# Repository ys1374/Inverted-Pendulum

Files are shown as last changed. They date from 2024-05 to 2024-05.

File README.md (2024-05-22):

The importance of automatic control in industries and everyday life is undeniable, and it can be said that 
automatic control systems are among the most important parts of today's advanced industries. In this 
project, we will pose a question and use tools such as dynamics and control science to find a satisfactory 
answer. Although this question has been repeatedly addressed in the field of control science and has 
received satisfactory answers, the nature of science and scientific methods is reproducibility. We aim to 
reproduce an answer to this issue in both theoretical and practical states. The question is: 
"How can the relative angle of a satellite carrier to the ground be controlled?" 
The need to pose such a question arises when you want to actively control the satellite carrier's angle 
relative to the ground to eliminate the effects of unmeasurable and unpredictable external factors such 
as wind or gravity. This can be done in two ways: one is using side fins, which will consume a lot of fuel 
since satellite carriers usually have to move at angles other than 90 degrees to the ground. Weight is 
always a critical factor for the satellite carrier's range. The other method is thrust vector control, which 
is the method examined in this project. In this project, we first define the satellite carrier model and 
derive the equations describing the satellite carrier's motion, then we use control science to control the 
main variable, i.e., the satellite carrier's angle relative to the ground.

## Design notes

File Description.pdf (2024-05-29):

### 1 Table of Contents

### 2 Introduction

The importance of automatic control in industries and everyday life is undeniable, and it can be said that automatic control systems are among the most important parts of today's advanced industries. In this project, we will pose a question and use tools such as dynamics and control science to find a satisfactory answer. Although this question has been repeatedly addressed in the field of control science and has received satisfactory answers, the nature of science and scientific methods is reproducibility. We aim to reproduce an answer to this issue in both theoretical and practical states. The question is:

"How can the relative angle of a satellite carrier to the ground be controlled?"

The need to pose such a question arises when you want to actively control the satellite carrier's angle relative to the ground to eliminate the effects of unmeasurable and unpredictable external factors such as wind or gravity. This can be done in two ways: one is using side fins, which will consume a lot of fuel since satellite carriers usually have to move at angles other than 90 degrees to the ground. Weight is always a critical factor for the satellite carrier's range. The other method is thrust vector control, which is the method examined in this project. In this project, we first define the satellite carrier model and derive the equations describing the satellite carrier's motion, then we use control science to control the main variable, i.e., the satellite carrier's angle relative to the ground.

### 3 Satellite Carrier Model

In this project, we consider the model as a pendulum representing the satellite carrier. This model provides a reasonably accurate approximation due to similar geometric features (one dimension being significantly larger than the other two) and a nearly balanced mass distribution along the pendulum length. For the forces exerted on the satellite carrier due to thrust vector changes, we consider a cart or carrier. Here, for simplicity in providing rotational force with common motors in the market compared to the linear motion of the cart requiring a rail and force transmission process, we consider the cart as a carrying rod and connect the pendulum to the carrying rod via an encoder (an encoder measures the angle error of the pendulum relative to the ground or the feedback sensor). The carrying rod plays the role of the cart and provides the force exerted on the satellite carrier due to thrust angle changes via a DC motor. Obviously, in this project, we consider the problem in 2D, but the results can be easily generalized to the real 3D state.

### 4 Derivation of Equations

### 4.1 Pendulum

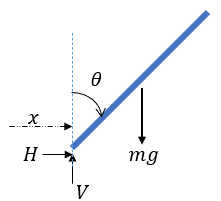
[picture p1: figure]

Figure 1

Pendulum lengtℎ = 2L

xg = x + Lsinθ | (1)
yg = Lcosθ | (2)
Jθ̈= ∑ T | (3)
max = H | (4)
may = V − mg | (5)

max = H → m

d

2xg
dt

2 = H

(1)
→ | mẍ+ m(Lsinθ)
'' = H | (6)

may = V − mg → m

d

2yg
dt

2 = V − mg

(2)
→ | 0 = V − mg | (7)

Since we write the rod rotation equation around its center of mass and there is complete symmetry around the center of mass, J = 0. Therefore, equation (3) with the help of equation (7) is summarized as equation (8):

J = 0

(3)
→ | 0 = ∑T → | 0 = HLcosθ − VLsinθ

(7)
→ H = mg

sinθ
cosθ

(8)

Now, we write the torques around the center of mass, resulting in the simplification of equation (3) as equation (9):

ẍ+ L(sinθ)

'' = g

sinθ
cosθ

(9)

### 4.2 Rod

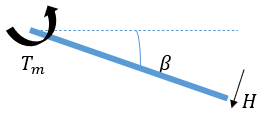
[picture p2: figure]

Figure 2

Rod lengtℎ = L

′

Jβ̈+ b0β̇ = ∑ T (10)

In equation (10), the friction coefficient b0 is considered for mechanical friction.

x = βL

′
(11)

### 4.3 DC Motor

Figure 3

La

dia
dt + Raia + Kbβ̇ = ea
(12)

In cylindrical DC motors (cross-section significantly smaller than length), La can be approximated as zero, making the equation a second-order function and simplifying the solution. Also, in these DC motors, the torque and back EMF constants are equal.

La = 0
Tm = KTia | (13)
Kb = KT = K
Raia + Kβ̇ = ea
| (14)

### 4.4 Motor and Rod Assembly

(10), (11) → Jβ̈+ b0β̇ = Tm − HL ′

(13)
→

J
K

β̈+

b0
K

β̇ +

HL

′
K

= ia (15)

(14), (15) → Ra(Jβ̈+ b0β̇ + HL
′
) + K

2β̇ = Kea → RaJβ̈+ (Rab0 + K
2

)β̇ + RaL
′H = Kea

→ RaJβ̈+ (Rab0 + K
2

)β̇ + RaL
′
(mẍ+ mL(sinθ)

'') = Kea →

RaJβ̈+ (Rab0 + K
2

)β̇ + RaL

′2
mβ̈+ RamLL
′
(sinθ)

'' = Kea →

(RaJ + RaL

′2
m)β̈+ (Rab0 + K
2

)β̇ + RamLL
′
(sinθ)

'' = Kea (16)

### 4.5 System Characteristic Equations (Nonlinear Equations)

L

′β̈+ L(sinθ)
'' = g

sinθ
cosθ (9)

(RaJ + RaL

′2
m)β̈+ (Rab0 + K
2

)β̇ + RamLL
′
(sinθ)

'' = Kea (16)

(sinθ)

'' = θ̈cosθ − θ̇sinθ (17)

(9)

(17)
→ L

′β̈+ Lθ̈cosθ − Lθ̇sinθ = g

sinθ
cosθ (18)

(16)

(17)
→ | (RaJ + RaL

′2
m)β̈+ (Rab0 + K
2

)β̇ + RamLL
′θ̈cosθ − RamLL

′θ̇sinθ = Kea (19)

(18) → θ̈=

gsinθ
Lcos²θ

+

sinθ
cosθ θ̇ −

L

′
Lcosθ β̈ (20)
(19) → β̈=

K
RaJ+RaL

′

2m

ea −

(Rab0+K

2
)
RaJ+RaL

′

2m

β̇ −

RamLL

′

RaJ+RaL

′

2m

θ̈cosθ +

RamLL

′

RaJ+RaL

′

2m

θ̇sinθ (21)

(20), (21) →

θ̈=

gsinθ
Lcos²θ

+

sinθ
cosθ θ̇

−

L

′
Lcosθ (
K
RaJ + RaL

′2m

ea −

(Rab0 + K

2
)
RaJ + RaL

′2m

β̇ −

RamLL

′
RaJ + RaL

′2m

θ̈cosθ

+

RamLL

′
RaJ + RaL

′2m

θ̇sinθ )

(21), (20) →

β̈=

K
RaJ + RaL

′2m

ea −

(Rab0 + K

2
)
RaJ + RaL

′2m

β̇ −

RamLL

′
RaJ + RaL

′2m

(
gsinθ
Lcosθ + θ̇sinθ −

L

′
L

β̈)

+

RamLL

′
RaJ + RaL

′2m

θ̇sinθ

Simplification

θ̈=

gsinθ
Lcos²θ

+

sinθ
cosθ θ̇ −

KL

′
L(RaJ + RaL

′2m)

ea
cosθ +

L

′
(Rab0 + K

2
)
L(RaJ + RaL

′2m)

β̇
cosθ +

RamL

′2

RaJ + RaL

′2m

θ̈

−

RamL

′2

RaJ + RaL

′2m

θ̇sinθ
cosθ

β̈=

K
RaJ + RaL

′2m

ea −

(Rab0 + K

2
)
RaJ + RaL

′2m

β̇ −

gRamL

′
RaJ + RaL

′2m

sinθ
cosθ −

RamLL

′
RaJ + RaL

′2m

θ̇sinθ

+

RamL

′2

RaJ + RaL

′2m

β̈+

RamLL

′
RaJ + RaL

′2m

θ̇sinθ

Simplification

θ̈=

RaJ + RaL

′2
m
RaJ

gsinθ
Lcos²θ

−

θ̇sinθ
cosθ −

KL

′
RaJL

ea
cosθ +

L

′
(Rab0 + K

2
)
RaJL

β̇
cosθ

β̈=

K
RaJ

ea −

(Rab0 + K

2
)
RaJ

β̇ −

gmL

′
J

sinθ
cosθ −

mLL

′
J

θ̇sinθ +

mLL

′
J

θ̇sinθ

Simplified characteristic equations (nonlinear equations):

θ̈ =

J + L

′2
m
J

gsinθ
Lcos²θ

−

θ̇sinθ
cosθ −

KL

′
RaJL

ea
cosθ

+

L | ′ | 2 | ) | β̇
(Rab0 | + K
RaJL

cosθ

(22)

β̈ | =
K | 2 | ) | gmL | ′ sinθ
RaJ

ea −

(Rab0 + K
RaJ

β̇ −
J

cosθ

(23)

We use equations (22) and (23) to plot the pendulum and demonstrate its motion in MATLAB.

### 4.6 System Characteristic Equations (Linear Equations)

Linearization of equations (22) and (23):

Assumption: sinθ = θ , cosθ = 1 , θθ̇ = 0

θ̈ =

g(J + L

′2
m)
LJ θ +

L

′
(Rab0 + K

2
)
LRaJ

β̇ −

KL

′
LRaJ

ea

(24)

β̈ = −

gmL

′
J

θ −

(Rab0+K²)

̇
RaJ

β̇ +

K
RaJ

ea

(25)

θ̈ = A1 θ + A2 β̇ + B1 ea
(26)
β̈= A3 θ + A4 β̇ + B2 ea
(27)

A1 =

g(J + L

′2
m)
LJ | A1 =

g(J + L

′2
m)
LJ

A3 = −

gmL

′
J

A4 = −

(Rab0 + K

2
)
RaJ | B1 = −

KL

′
LRaJ

B2 =

K
RaJ

### 4.7 State-Space Equations (Linear Equations)

To design the controller, we first convert the equations to their state-space form and obtain the system in state-space representation. Therefore, from equations (26) and (27), we have:

ẋ = Ax + Bea | (28)
ẋ = [

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
] x + [

0
B1
0
B2

] ea
| (29)

ẋ = [

x1̇
x2̇
x3̇
x4̇

] = [

x2
θ̈
x4
β̈

] x = [

θ
θ̇
β
β̇

] = [

x1
x2
x3
x4

] A = [

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
] | B = [

0
| B1
0
| B2

]

### 5 Fabrication of the dynamic model

### 5.1 Specifications of the Fabricated model

L

′ = 0.28 m | #Rod length
L = 0.11 m | #half Pendulum length
g = 9.81 | #Gravity constant

K =

0.588
7.8
N. m A | #DC motor torque constant
Ra = 3 Ω | # DC motor resistance
b0 = 0.1 | #Mechanical resistance
m = 0.039 Kg | # Pendulum weight

### 5.2 Components used

The following components were used in the construction of this project:

1) 24V DC servo motor, model Yaskawa UGFMED-B5LGR51
2) Arduino Mega 2560
3) Autonics 2500 pulse encoder
4) DC motor driver 43A 27V, model BTS7960
5) 12V power supply (Arduino power supply)
6) 24V 10A power supply
7) Breadboard
8) Mounting plates and connecting rods

### 5.3 State-space equations for the real model (linear equations)

From equations (26) and (27) and obtaining their coefficients, we have:

ẋ = [

0
102.75
0
−5.33

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
| 12.9
| 1 −5.07 ] x + [
| 0
| 3.18
| 0 −1.25

] ea

A1 = 102.75 | A2 = 12.9 | A3 = −5.33 | A4 = −5.07 | B1 = 3.18 | B2 = −1.25

### 5.4 Fabrication Challenges

During the construction of the project, we encountered several issues which I'll detail here.

1) Encoder Signal: The signal B from the encoder, which represents the theta feedback (angle of the pendulum), was a square wave signal that reached a maximum approximate voltage of 1.7 volts. However, Arduino considers a minimum of 3 volts for high signals (or logic level '1'). Due to this voltage difference, Arduino couldn't accurately detect the angle or direction of rotation. This issue was resolved by adding a 1.5V AAA battery to compensate for the voltage difference.

2) Arduino Uno Limitations: Initially, we used the Arduino Uno controller, which, due to having only one pair of signal inputs for the encoder, couldn't provide a solution to our problem. This limitation was overcome by replacing it with the Arduino Mega controller.
3) Length of Lever Arm: The significant length of the lever arm caused increased sensitivity in the motor operation, leading to motor inertia issues. By minimizing the length of this lever arm, we were able to mitigate this problem.
4) Angular Refresh Rate: One fundamental issue we faced was the refresh rate of the pendulum angle. By reducing the refresh time to 1 millisecond, we initially achieved active control. However, these changes had an irreversible negative impact on the motor driver. With a refresh rate of 1 millisecond, the right-side H-bridge of the motor driver completely failed. This issue was resolved by replacing the motor driver and increasing the refresh rate to 10 milliseconds.

### 5.5 Wiring diagram of the constructed model

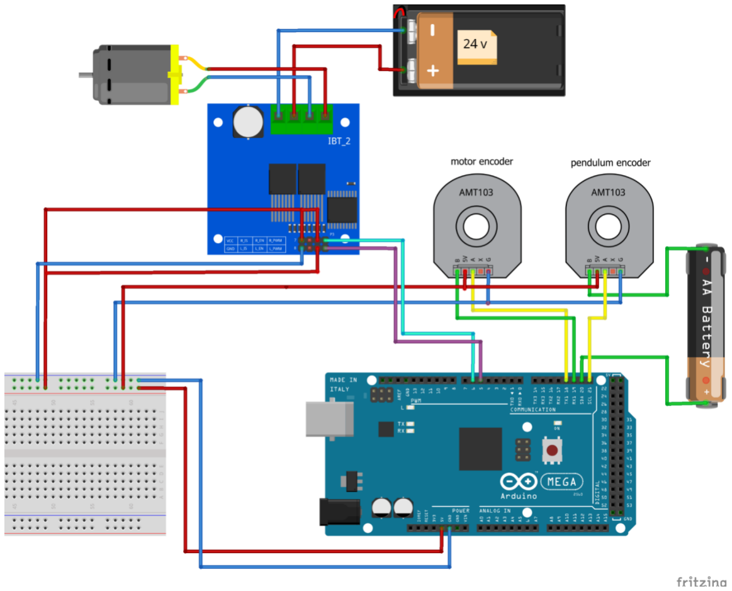
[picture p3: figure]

Figure 4

### 6 Simulation

### 6.1 Root Locus Analysis

The Root Locus Analysis of the closed-loop poles of the system can be observed in Figure 5.

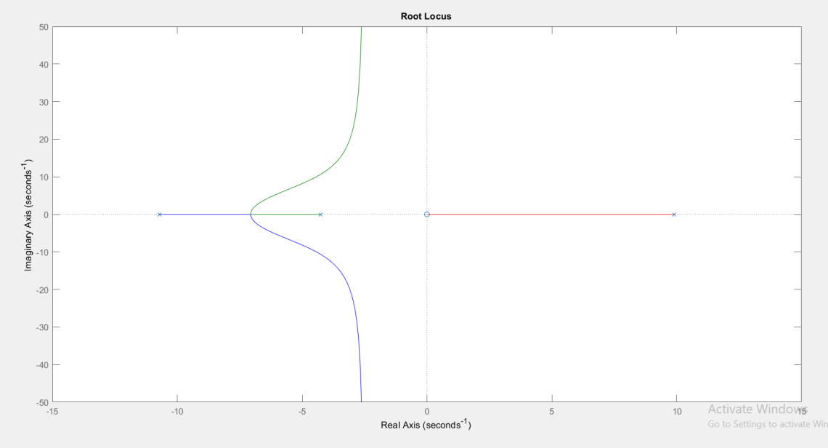
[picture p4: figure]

Figure 5*

* Figure 5* is obtained from the MATLAB code in the attached file root_locus.m.

The Fabricated Model has 4 poles at [0, 9.91, -10.72, -4.26] and two zeros at [0, 0].

### 6.2 Proportional Controller

We will use proportional control using state-space, where the controller coefficients are obtained from the LQR method with cost functions and weights (R) and (Q). With this method, we obtain 4 coefficients for the controller, each corresponding to its respective state variable ((θ, θ̇

, β, β̇)). In state
feedback, we feedback the variables and compare them with their desired values, then subtract them. Afterwards, we multiply this difference by the control coefficients. This process generates the necessary control force signal to control the system or neutralize disturbances.

To visualize the position and response of the system in MATLAB, we use two functions: `nonlinear_sys.m` and `print_sys.m`, which encompass the characteristic functions of the nonlinear system. The files are attached. You can also refer to the MATLAB file `system.m` to see how the pendulum moves and execute it.

The folloing figures demonstrate this design.

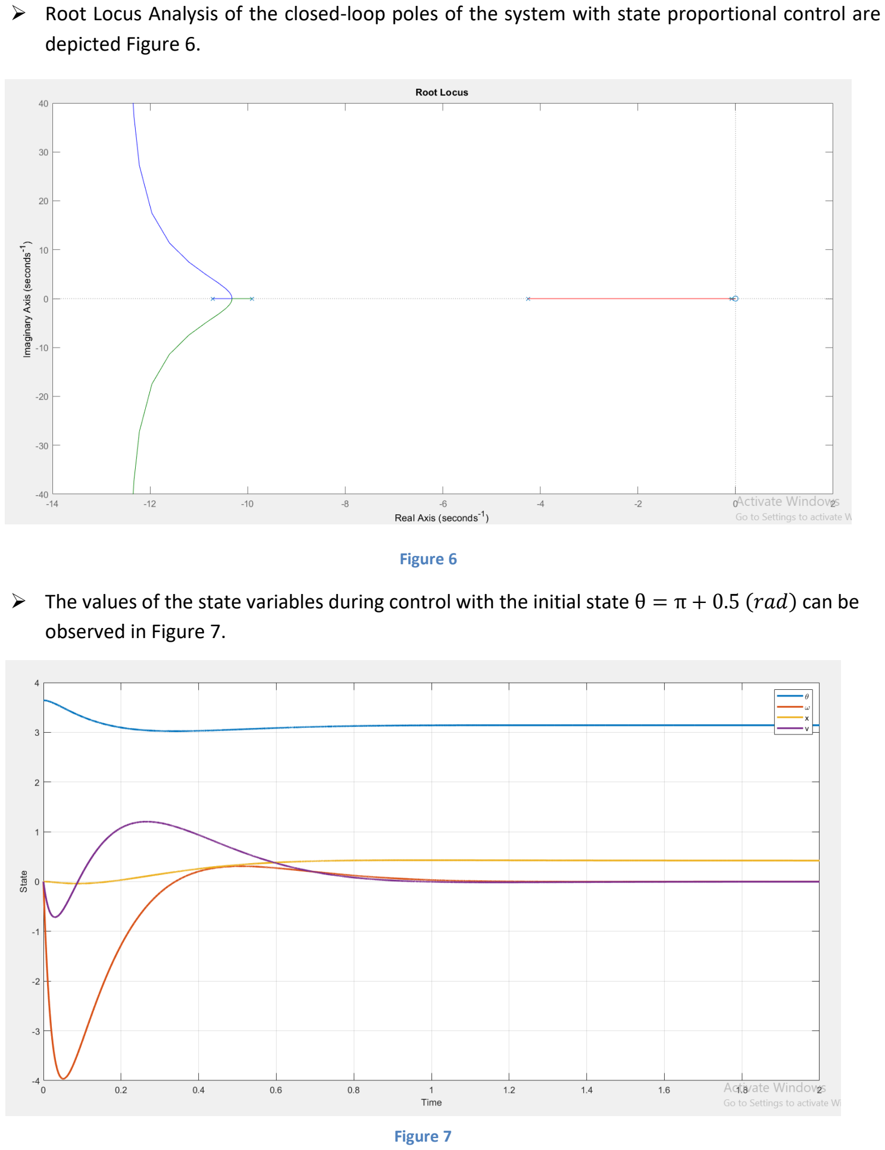
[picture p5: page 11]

- Root Locus Analysis of the closed-loop poles of the system with state proportional control are depicted Figure 6.

Figure 6

- The values of the state variables during control with the initial state θ = π + 0.5 (rad) can be observed in Figure 7.

Figure 7

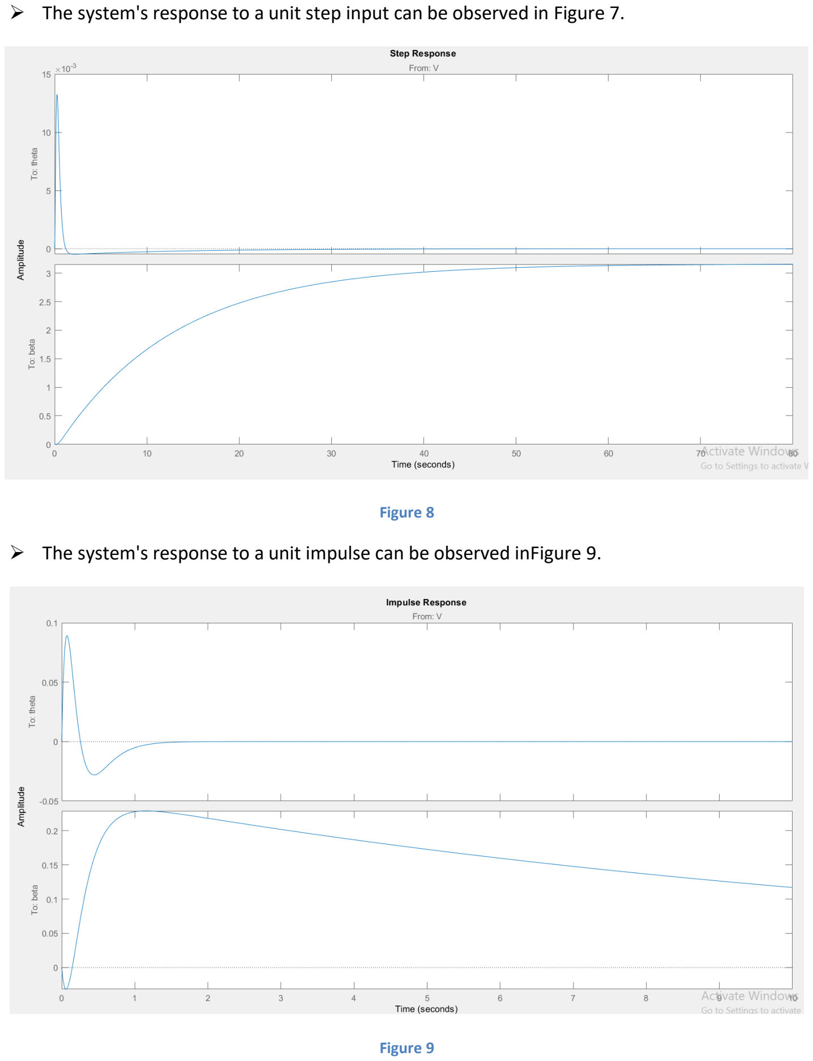
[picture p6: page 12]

- The system's response to a unit step input can be observed in Figure 7.

Figure 8

- The system's response to a unit impulse can be observed inFigure 9.

Figure 9

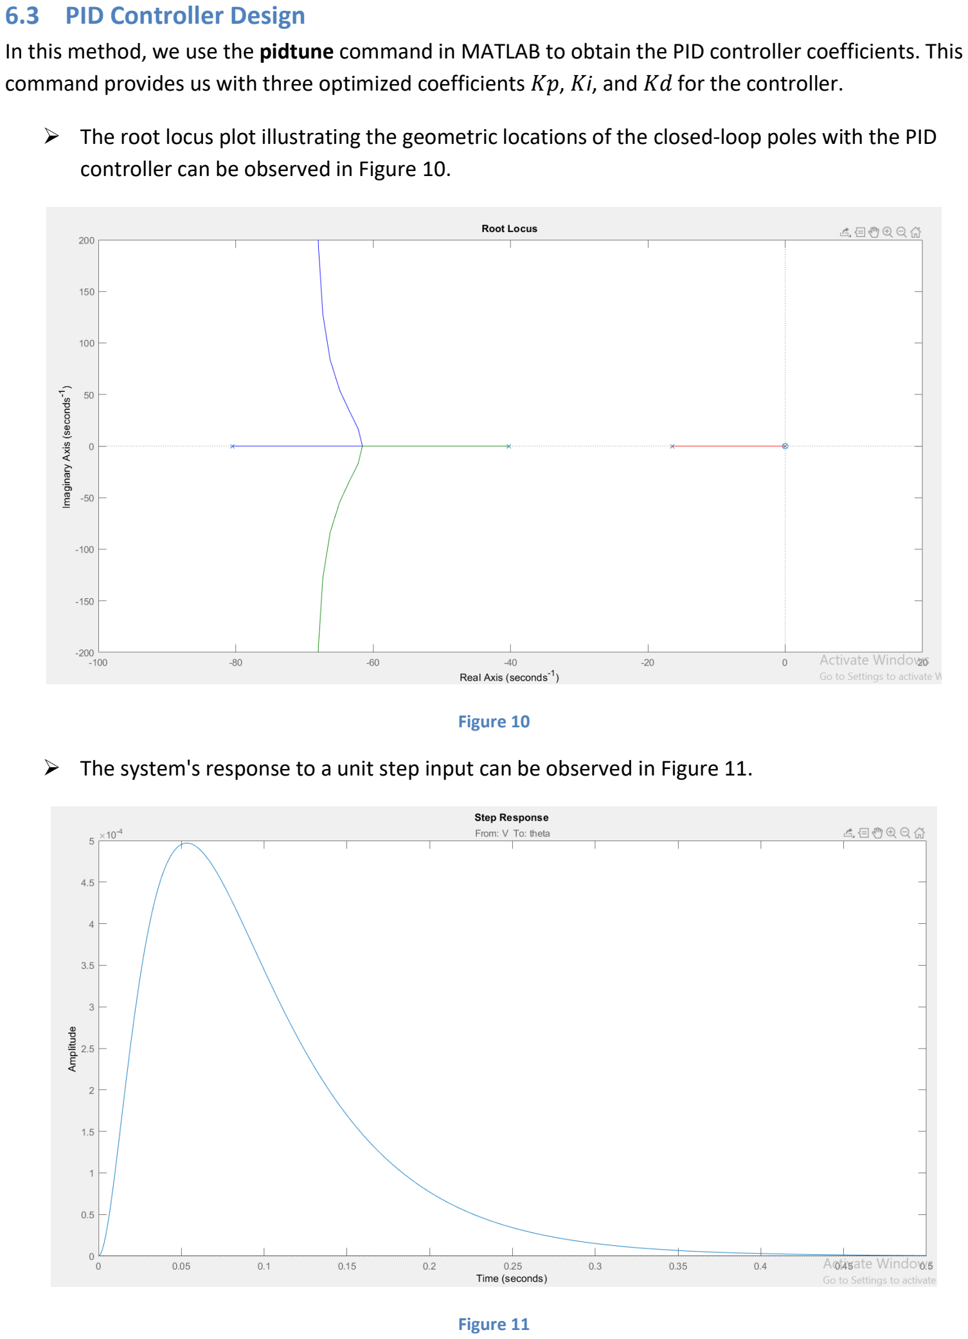
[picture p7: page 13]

### 6.3 PID Controller Design

In this method, we use the pidtune command in MATLAB to obtain the PID controller coefficients. This command provides us with three optimized coefficients Kp, Ki, and Kd for the controller.

- The root locus plot illustrating the geometric locations of the closed-loop poles with the PID controller can be observed in Figure 10.

Figure 10

- The system's response to a unit step input can be observed in Figure 11.

Figure 11

- The system's response to a unit impulse can be observed in Figure 12.

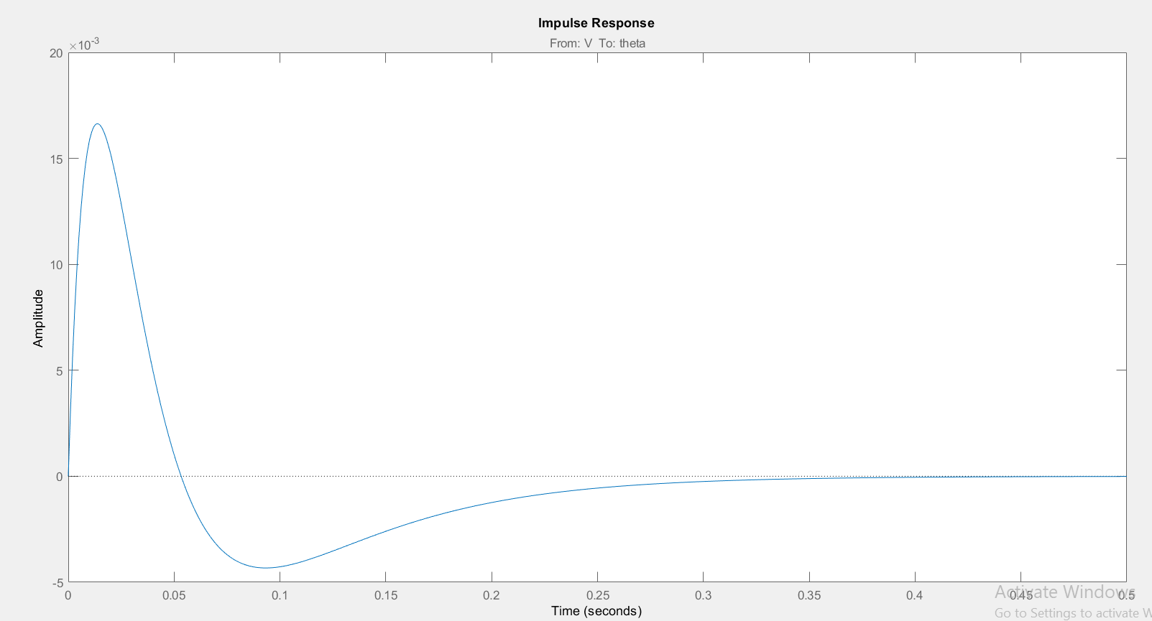
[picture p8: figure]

Figure 12

### 7 Conclusion

Initially, we modeled the satellite carrier into a more accessible model, like an inverted pendulum. Then, using the dynamics equations of the pendulum, we simulated the applied force through angle adjustment of the thrusters using a rod and a DC motor model. We extracted the equations for both through dynamics and electrical machinery. Now, we have access to the controller's tuning function, namely the motor voltage, and the output, namely the pendulum angle. We then proceed to design the controller. The controller we use is PID, and we obtained its three coefficients using the `pidtune` command in MATLAB. Now, it's time to apply this controller to our constructed dynamic model. We apply the three controller coefficients using the PID Arduino library to the Mega Arduino controller, and we observe that the controller effectively maintains the carrier upright. In this project, we have achieved our desired outcome, which is reproducing the response given to the carrier angle control.

### 8 References

[1]Steven L. Brunton, J. Nathan Kutz - Data-Driven Science and Engineering_ Machine Learning, Dynamical Systems, and Control-Cambridge University Press (2019)

[2] Dynamics / J. L. Meriam, L. G. Kraige, Virginia Polytechnic Institute and State University, J. N. Bolton, Bluefi eld State College.—Eighth edition.
[3] Modern Operating Systems By Andrew S. Tanenbaum(5th Edition) by Katsuhiko Ogata, Andrew S. TanenbaumHardcover, 912 Pages, Published 2009 by Prentice Hall

[4] Advanced Engineering Mathematics, 10th Edition by ERWIN KREYSZIG, HERBERT KREYSZIG,New York, New York,EDWARD J. NORMINTON,Associate Professor of Mathematics, Carleton UniversityProfessor of Mathematics,Ohio State UniversityColumbus , JOHN WILEY & SONS, INC.
[5] James K. Roberge. The mechanical seal. Bachelor's thesis, Massachusetts Institute of Technology, May 1960.
[6] Differential Equations", Dr. Masoud Nikoukar, Azadeh Publications, AmirKabir University of Technology.

### 9 Appendix

1) \Arduino code\inverted_pendulum.ino
2) \Matlab code\noneliniar_sys.m
3) \Matlab code\print_sys.m
4) \Matlab code\root_locus.m
5) \Matlab code\sys2.m
6) \Matlab code\system.m
7) \Matlab code\system_pid.m

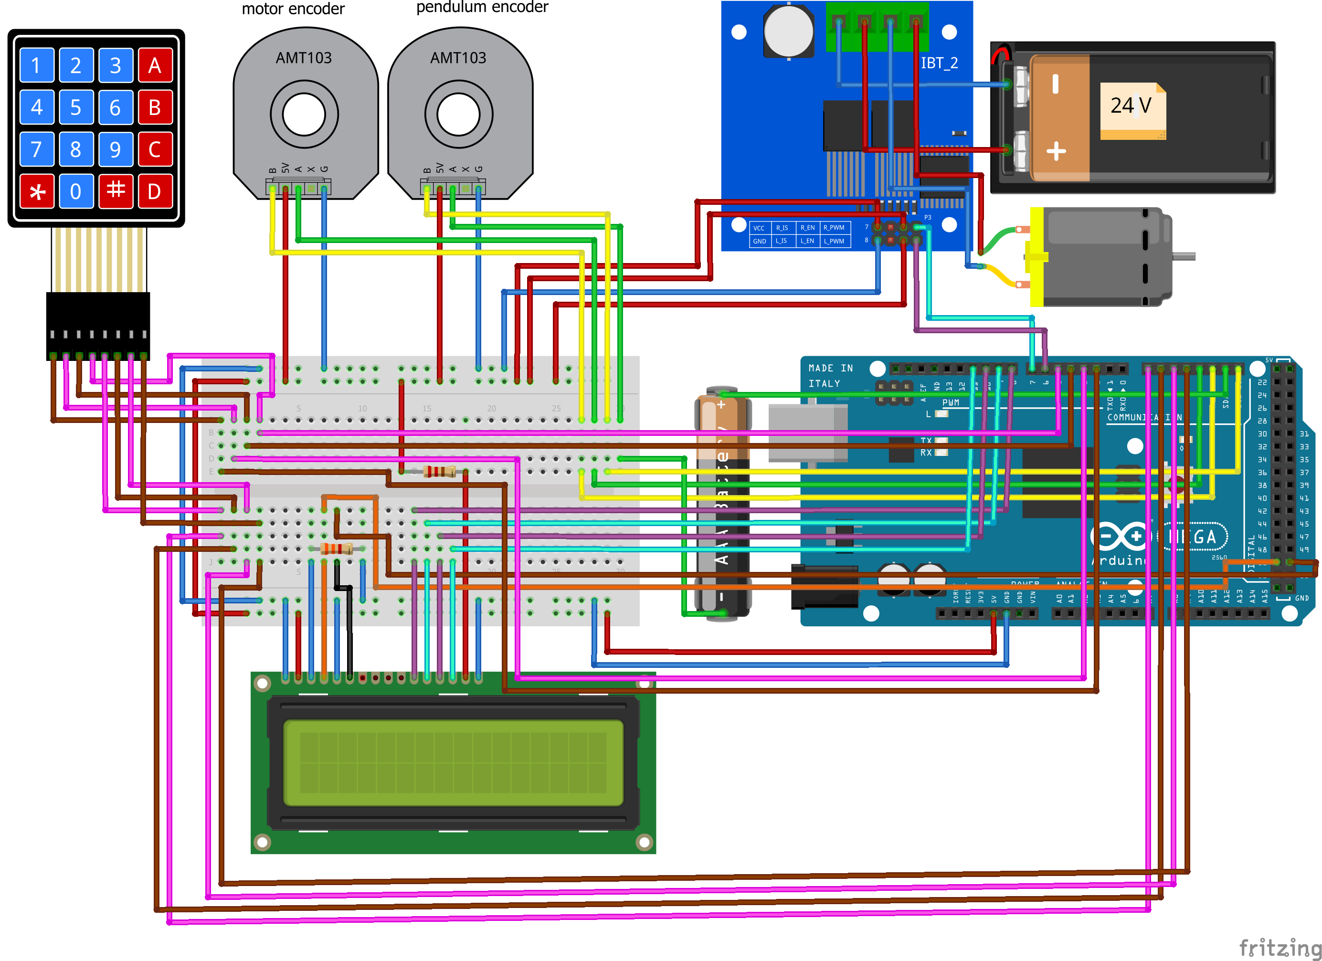
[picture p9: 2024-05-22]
PDF photo/Untitled Sketch_bb.png

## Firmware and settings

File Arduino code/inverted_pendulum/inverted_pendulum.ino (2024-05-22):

// !!!!!!!!!!!!!!!!DO NOT CHANGE ANYTHING !!!!!!!!!!!!!!
// © 2021 All rights reserved for Yasin Salehi
//if you change even a dot in this script
//i won't stay down i'll bring you to marshall court
//and i beat you there then i will feed you to the SHARKS!!!!!
//HA HA HA HA HA ....  
//oh my god did you just believe that?
//HA HA HA HA HA ....
//i'm so funny oh lord...
//pardon my sense of humor of course you can change anything 
//but i recommendyou not to do so
//i wrote the script myself and now i don't even know what is it about
//anyway if you made any improvement by NOT CHANGEING the script
//feel free to write to me
//salehi.yasin@gmail.com
//Salehi-REGARDS
//stay safe - wear mask
























//-----------------------------------------------------
#include <Encoder.h>
#include <PID_v1.h>
#include <LiquidCrystal.h>
#include <Keypad.h>

char hexaKeys[4][4] = {  {1, 2, 3, 13}, {4, 5, 6, 14}, {7, 8, 9, 15}, {11, 10, 12, 16}};
byte rowPins[4] =  {14, 15, 16, 17};
byte colPins[4] = {2, 3, 4, 5};
const int m = 5;
const int n = m - 1;
int k_triger = 0;
int cruser_column;
int chose = 0;

double theta = 0;
double theta_Setpoint = 0;
double Voltage;
double theta_kp, theta_ki, theta_kd;
double beta = 0;
double beta_Setpoint = 0;
double beta_kp = 1.25, beta_ki = 0, beta_kd = .1;

int time1 = 11;

Encoder pend_encoder(18, 19);
Encoder rod_encoder(20, 21);

PID theta_controller(&theta, &Voltage, &theta_Setpoint, theta_kp, theta_ki, theta_kd, DIRECT);
PID beta_controller(&beta, &theta_Setpoint, &beta_Setpoint, beta_kp, beta_ki, beta_kd, DIRECT);

LiquidCrystal lcd(50, 51, 8, 9, 10, 11);

Keypad customKeypad = Keypad(makeKeymap(hexaKeys), rowPins, colPins, 4, 4);

void setup() {

  Serial.begin(115200);

  lcd.begin(20, 4);

  pinMode(6, OUTPUT);
  pinMode(7, OUTPUT);

  lcd_first_print();
  defult_chose();
  controller_asignment();
    lcd.clear();
  while (time1 > 0) {
    time1 = time1 - 1;
        
    lcd.setCursor(4, 0);
    lcd.print("**WARNING**");
    lcd.setCursor(2, 1);
    lcd.print("The Process will");
        lcd.setCursor(6, 2);
    lcd.print("start in");
    lcd.setCursor(9, 3);
    lcd.print(time1);
    delay(1000);
    lcd.clear();
  }

  pend_encoder.write(5000);
  rotation_180();

    lcd.setCursor(4, 0);
    lcd.print("**WARNING**");
    lcd.setCursor(2, 1);
    lcd.print("Please DO NOT let");
        lcd.setCursor(0, 2);
    lcd.print("full cycle rotation");
    lcd.setCursor(5, 3);
    lcd.print("DISTURB IT");


}
void loop() {

  theta = pend_encoder.read();
  beta = rod_encoder.read();


  if (-1000 < theta & theta < 1000)
  {
    theta_controller.Compute();

    assign_Voltage_fun(Voltage);
    print_simple();

  }
  else
  {

    turn_stop();//-----------------------------------------
  }
}
//********************************************************************************
//***************************FUNCTIONS 1st part***********************************
//********************************************************************************

void turn_cw(int value) {
  analogWrite(6, value);
  analogWrite(7, 0);
}

void turn_ccw(int value) {
  analogWrite(6, 0);
  analogWrite(7, value);
}

void turn_stop() {
  analogWrite(6, 0);
  analogWrite(7, 0);
}
//--------------------------------
void assign_Voltage_fun(double Voltage_fun) {
  if (Voltage_fun < 1 & Voltage_fun > -1) {
    turn_stop;
  }
  if (Voltage_fun >= 1) {
    turn_cw(Voltage_fun);
  }
  if (Voltage_fun <= -1) {
    turn_ccw(abs(Voltage_fun));
  }
}
//------------------------------------
void print_simple() {
  Serial.print(theta) ;
  Serial.print("|||||||") ;
  Serial.print(beta) ;
  Serial.print("|||||||") ;
  Serial.print(theta_Setpoint) ;
  Serial.println("") ;
}
//------------------------------------
void rotation_180() {
  pend_encoder.write(5000);
  int theta_func;
  int beta_func;
  theta_func = pend_encoder.read();
  while (theta_func < 9000 &  theta_func > 1000) {
    theta_func = pend_encoder.read();
    beta_func = rod_encoder.read();

    while (beta_func != 50) {
      beta_func = rod_encoder.read();
      turn_cw(80);

      theta_func = pend_encoder.read();
      if (theta_func == 9000 || theta_func == 1000) {
        if (theta_func == 9000) {
          pend_encoder.write(-1000);
        }
        if (theta_func == -9000) {
          pend_encoder.write(1000);
        }
        return;
      }
    }

    while (beta_func != 0) {
      beta_func = rod_encoder.read();
      turn_ccw(200);
      theta_func = pend_encoder.read();
      if (theta_func == 9000 || theta_func == 1000) {
        if (theta_func == 9000) {
          pend_encoder.write(-1000);
        }
        if (theta_func == -9000) {
          pend_encoder.write(1000);
        }
        return;
      }
    }

  }
}
//------------------------------------------------------
void controller_asignment() {
  theta_controller.SetMode(AUTOMATIC);
  theta_controller.SetOutputLimits(-255, 255);
  theta_controller.SetSampleTime(10);
  theta_controller.SetTunings(theta_kp, theta_ki, theta_kd);

  beta_controller.SetMode(AUTOMATIC);
  beta_controller.SetOutputLimits(-150, +150);
  beta_controller.SetSampleTime(3);
  beta_controller.SetTunings(beta_kp, beta_ki, beta_kd);
}

//********************************************************************************
//***************************FUNCTIONS 2nd part***********************************
//********************************************************************************

//FUNCTION read k value from keypad  --------------------------------------------
double k(int cruser_row) {
  double k1, k2, k;
  int k1_digits[m] = {0};
  int k1_digits_old[m] = {0};

  int k2_digits[m] = {0};
  int k2_digits_old[m] = {0};

  int oldkey  = 0;
  int exit_1  = 0;
  int dot_key = 0;
  int p = 0;
  int lcd_cruser = 4;


  while (exit_1 == 0) {

    int Key_k = customKeypad.getKey();

    if (Key_k != 0 & Key_k == 12) {
      exit_1 = exit_1 + 1;
      Serial.println("12 is pushed");
      delay(500);
    }
    if (Key_k != 0  & Key_k == 11) {
      lcd.setCursor(lcd_cruser, cruser_row);
      lcd.print(".");
      dot_key = dot_key + 1;
      Serial.println("11 is pushed");
      delay(500);
    }


    // >1 digits---------------------------------------------------
    if (Key_k != 0 & dot_key == 0) {

      //push 1-9 number keys(key 1-9)------------------------------
      if (Key_k < 10) {
        lcd.setCursor(lcd_cruser, cruser_row);
        lcd.print(Key_k);
        k1_digits[0] = Key_k;

        for (int i = 0; i < n ; i++) {
          k1_digits[i + 1] = k1_digits_old[i];
        }


        for (int j = 0; j < n + 1 ; j++) {
          k1_digits_old[j] = k1_digits[j];
        }


        for (int t = 0; t < n + 1; t++) {
          Serial.print(k1_digits[p]);
        }
        Serial.println("");

      }
      //push 0 number (key 10)------------------------------
      if (Key_k == 10) {
        k1_digits[0] = 0;
        lcd.setCursor(lcd_cruser, cruser_row);
        lcd.print(0);
        for (int i = 0; i < n ; i++) {
          k1_digits[i + 1] = k1_digits_old[i];
        }


        for (int j = 0; j < n + 1 ; j++) {
          k1_digits[j] = k1_digits_old[j];
        }


        for (int t = 0; t < n + 1; t++) {
          Serial.print(k1_digits[p]);
        }
        Serial.println("");

      }
      //--------------------------------------------------------
      k1 = k_1(k1_digits);
      delay(500);
      lcd_cruser = lcd_cruser + 1;

    }
    // 0< <1 digits------------------------------------------------------
    if (Key_k != 0  & dot_key == 1) {

      //push 1-9 number keys(key 1-9)------------------------------
      if (Key_k < 10) {

        lcd.setCursor(lcd_cruser, cruser_row);
        lcd.print(Key_k);

        k2_digits[p] = Key_k;
        p = p + 1;

        for (int i = 0; i < n + 1; i++) {
          Serial.print(k2_digits[i]);
        }
        Serial.println("");


      }
      //push 0 number (key 10)------------------------------
      if (Key_k == 10) {

        k2_digits[p] = 0;
        p = p + 1;

        lcd.setCursor(lcd_cruser, cruser_row);
        lcd.print(0);

        for (int i = 0; i < n + 1; i++) {
          Serial.print(k2_digits[i]);
        }
        Serial.println("");

      }
      //--------------------------------------------------------
      k2 = k_2(k2_digits);
      delay(500);
      lcd_cruser = lcd_cruser + 1;

    }
    //--------------------------------------------------------------
  }

  k =  k1 + k2;

  return k;

}
//FUNCTION tunrn digits to number for >1 numbers--------------------------------------------------------------
int k_1(int k_11[m]) {
  float num = k_11[0] + (k_11[1] * 1e1) + (k_11[2] * 1e2) + (k_11[3] * 1e3) + (k_11[4] * 1e4);
  return num;
}
//FUNCTION tunrn digits to number for 0< <1 numbers----------------------------------------------------------
double k_2(int k_22[m]) {
  double num;
  //  if (k_22[0] == 0 & k_22[1] == 0 & k_22[2] == 0 & k_22[3] == 0 & k_22[4] == 0) {
  //    return num = 0.0;
  //  }

  num = (k_22[0] / 1e1) + (k_22[1] / 1e2) + (k_22[2] / 1e3) + (k_22[3] / 1e4) + (k_22[4] / 1e5);
  return num;
}
//FUNCTION lcd first print -----------------------------------------------------------------------------------
void lcd_first_print() {
  lcd.setCursor(0, 0);
  lcd.print("B.Sc. Final Proj. of");

  lcd.setCursor(0, 2);
  lcd.print("YASIN SALEHI");

  lcd.setCursor(0, 3);
  lcd.print("1398-1400");

  delay(7000);
  lcd.clear();
  lcd.setCursor(0, 0);
  lcd.print("Donated to");

  lcd.setCursor(0, 2);
  lcd.print("Kurdistan University");


  delay(5000);
  lcd.clear();
  lcd.setCursor(0, 0);
}
//FUNCTION get k values -----------------------------------------------------------------------------------
void get_k_values() {
  lcd.setCursor(0, 0);
  lcd.print("Please Enter K Gain ");
  lcd.setCursor(0, 1);
  lcd.print("Values");
  delay(3000);
  lcd.clear();

  if (k_triger == 0) {
    cruser_column = 0;
    lcd.setCursor(15, cruser_column); lcd.print("*10^3");
    lcd.setCursor(0, cruser_column);
    lcd.print("Kp=");
    theta_kp = k(cruser_column);
    k_triger = k_triger + 1;
    Serial.println(""); Serial.print("theta_kp is set"); Serial.print(theta_kp, 5); Serial.println("");
  }

  if (k_triger == 1) {
    cruser_column = 1;
    lcd.setCursor(15, cruser_column); lcd.print("*10^3");
    lcd.setCursor(0, cruser_column);
    lcd.print("Ki=");
    theta_ki = k(cruser_column);
    k_triger = k_triger + 1;
    Serial.println(""); Serial.print("theta_ki is set"); Serial.print(theta_ki, 5); Serial.println("");

  }


  if (k_triger == 2) {
    cruser_column = 2;
    lcd.setCursor(15, cruser_column); lcd.print("*10^3");
    lcd.setCursor(0, cruser_column);
    lcd.print("Kd=");
    theta_kd = k(cruser_column);
    k_triger = k_triger + 1;
    Serial.println(""); Serial.print("kd is set"); Serial.print(theta_kd, 5); Serial.println("");
  }
}

//FUNCTION defult K chose----------------------------
void defult_chose() {
  lcd.print("Do you whant to");
  lcd.setCursor(0, 1);
  lcd.print("Continue with defult");
  lcd.setCursor(0, 2);
  lcd.print("K Gain Values ?");
  lcd.setCursor(0, 3);
  lcd.print("Yes-->1  No-->2");

  while (chose < 1) {
    int Key = customKeypad.getKey();
    if (Key == 1) {
      lcd.clear();
      theta_kp = 1.2, theta_ki = .8, theta_kd = .05;
 //     theta_kp = 1.674, theta_ki = 16.872, theta_kd = .042;

      lcd.setCursor(0, 0);
      lcd.print("Kp= "); lcd.print(theta_kp);
      lcd.setCursor(15, 0); lcd.print("*10^3");
      lcd.setCursor(0, 1);
      lcd.print("Ki= "); lcd.print(theta_ki);
      lcd.setCursor(15, 1); lcd.print("*10^3");
      lcd.setCursor(0, 2);
      lcd.print("Kd= "); lcd.print(theta_kd);
      lcd.setCursor(15, 2); lcd.print("*10^3");
      delay(3000);

      chose = 1;
    }
    if (Key == 2) {
      lcd.clear();
      get_k_values();
      chose = 2;
    }
  }
}
